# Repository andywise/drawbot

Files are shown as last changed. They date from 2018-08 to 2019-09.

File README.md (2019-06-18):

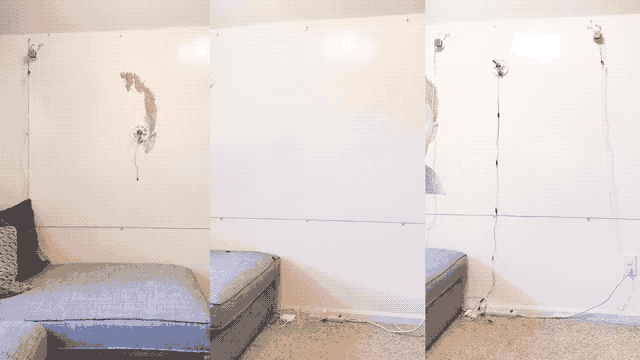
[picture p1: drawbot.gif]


# Drawbot ✏️🤖

Drawing robot capable of rendering SVG paths over WebSockets. Powered by a Raspberry Pi running Node.js.

## Parts List
### Printable Parts
* [Motor Mounts](https://www.thingiverse.com/thing:3054707) (two of each)
* [Electronics Case](https://www.thingiverse.com/thing:3058312)
* [Pen Holder Gondola](https://www.thingiverse.com/thing:372244)
* [Servo Horn Extension](https://www.thingiverse.com/thing:2427037)

### Everything Else (~$150 or less)

* [NEMA 17 Stepper Motors, 36.8oz.in 12v 0.4a](https://www.amazon.com/Stepping-Motor-26Ncm-36-8oz-Printer/dp/B00PNEQ9T4) (need 2) - $23.98
* [Suction Cup with Quick Release](https://www.harborfreight.com/suction-cup-with-quick-release-62715.html) (x2) - $5.98
* [Spiderwire 80-pound fishing line](https://www.amazon.com/gp/product/B00LDYLVVO/ref=oh_aui_search_detailpage?ie=UTF8&psc=1) - $17.56
* [Micro USB cable 10-ft. 2-pack](https://www.amazon.com/Android-Extremely-Durable-Charging-Generation/dp/B01NAG0YPD/ref=sr_1_8) - $8.99
* [Micro USB breakout 10-pcs](https://www.amazon.com/MagiDeal-10pcs-Female-Pinboard-2-54mm/dp/B0183KF7TM/ref=sr_1_4) (only need 2) - $6.59
* [USB type a female breakout 2-pack](https://www.ebay.com/itm/USB-2-0-Type-A-Female-Breakout-Board-2-54mm-Header-Gold-plated-Pack-of-2/302540094106) - $4.50
* [Raspberry Pi Zero W](http://www.microcenter.com/product/486575/Zero_W) - $10)
* [Easydriver Stepper Motor Driver](https://www.amazon.com/Cylewet-Easydriver-Stepper-Headers-Screwdriver/dp/B073D4H4F4/ref=sr_1_cc_1) (2-pack) - $9.99
* [SG92R](http://www.microcenter.com/product/454408/Micro_Servo) Micro Servo motor - $6.99
* [6003zz bearing 17x35x10](https://www.amazon.com/VXB-6003ZZ-Bearing-17x35x10-Shielded/dp/B002BBCO32/ref=sr_1_1) (need 2) - $11
* [10pcs 500mm 3-pin servo extensions](https://www.amazon.com/White-Terminal-Female-Extension-Airplane/dp/B01HLUZO4S/) (need several) - $7.69
* [2.1mm x 5.5mm barrel jack 15pcs](https://www.amazon.com/15PCS-Power-Socket-Barrel-Type-DC-005/dp/B00W944ACE/ref=sr_1_5) (need 1) - $7.59
* [12v 1a power adapter 2.1mm/5.5mm lead](https://www.amazon.com/Dericam-Power-Adapter-Supply-1000mA/dp/B01N3SNRE4/ref=sr_1_3) - $9.99
* [USB Micro Power Adapter](https://www.amazon.com/Keyestudio-Raspberry-Supply-Adapter-Charger/dp/B073RBXX2G/ref=sr_1_20) - $5.99
* [Pololu Universal Mounting Hub for 5mm shaft, #4-40 holes (2-pack)](https://www.pololu.com/product/1203) - $11.44
* [USB fan (40mm)](https://www.amazon.com/gp/product/B071JB9WYB/) - $7.99
* \#8-32 x 1-5/8 in. Eye Bolts (2-pack) - $0.98
* 8 screws for spools (#4-40 x ~½")
* 8 screws for motors (M3-.50 x 6mm metric machine screws)
* 1-2 small screws for gondola to secure pen/marker
* [Mounting Putty](https://www.amazon.com/Loctite-Fun-Tak-Mounting-2-Ounce-1087306/dp/B001F57ZPW) - $4.87
* Standard wire or jumper wires (and headers for components if using jumpers)
* Dry erase markers (or other drawing implements)
* Micro SD card (class 10 or better)

## Wiring

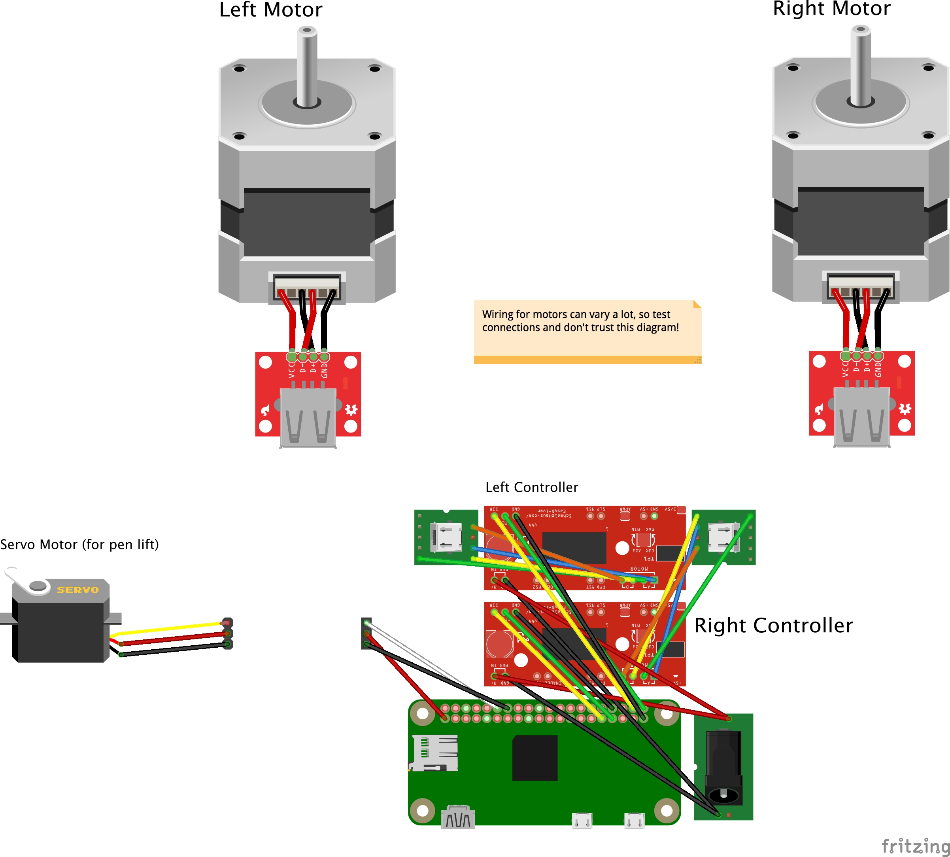
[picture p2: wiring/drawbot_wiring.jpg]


## Hardware Assembly

Thank you to the kind people at the Johnson County Library's Black & Veatch [MakerSpace](https://www.jocolibrary.org/makerspace) for documenting the assembly process at [instructables.com](https://www.instructables.com/id/Drawbot/).

## Raspberry Pi Zero W Basic Setup
1. **Download and install [Etcher](https://etcher.io/)**.
2. **Download and install latest [Raspbian OS](https://www.raspberrypi.org/downloads/raspbian/)** and flash it onto your SD card with Etcher.
3. **Enable SSH** by adding a blank file named `ssh` (no extension) to the `boot` directory on the Pi's SD card. (Last tested with Raspbian Stretch Lite 2018-06-27 version.)
4. **Set up Wifi** by adding a file named `wpa_supplicant.conf` to the same `boot` directory with the following contents (replace `MySSID` and `MyPassword` with your credentials):  
	```
	ctrl_interface=DIR=/var/run/wpa_supplicant GROUP=netdev
	update_config=1
		
	network={ 
		ssid="MySSID" 
		psk="MyPassword" 
	}
	```

## Software Prerequisites
From a device connected to the same network as the Drawbot Pi, SSH into the Pi with `ssh pi@raspberrypi.local`. The default password is `raspberry`.

Then, on the Drawbot Pi:

1. **Update, upgrade, and install NPM, Git.** (Automatically answer "yes" to everything.):
	* `sudo apt-get update`
	* `sudo apt-get upgrade`
	* `sudo apt-get install npm`
	* `sudo apt-get install git`

2. **Install Node.js.**
	* `sudo npm install -g n` (Install **n** for node.js version management. [github.com/tj/n](https://github.com/tj/n))
	* `sudo n stable` (Install latest stable version of Node.js. Last tested with v10.8.0)

3. **Upgrade NPM.** (and remove old apt-get version).
	* `sudo npm install npm@latest -g`
	* `sudo apt-get remove npm`
	* `sudo reboot` (After rebooting, you'll have to SSH into the Pi again.)

4. **Install pigpio C library.** [npmjs.com/package/pigpio](https://www.npmjs.com/package/pigpio)
	* `sudo apt-get install pigpio` (Only if you're using Raspbian *Lite*.)
	* `npm install pigpio`

## Installation
On the Drawbot Pi:

1. `git clone https://github.com/andywise/drawbot.git` to clone this repository.
2. `cd drawbot`
3. `npm i`

## Use
On the Drawbot Pi:

* Run `npm start` or `sudo node draw.js` to start the Drawbot controller.

## Controlling the Drawbot
On a device connected to the same local network as the Drawbot Pi:

* Go to [raspberrypi.local/control](http://raspberrypi.local/control) to access the Drawbot control interface.
* Use the "bullseye" interface to manually position the gondola, or raise/lower the pen/marker.
* Use the settings panel to configure the Drawbot's `D`, `X`, and `Y` values (see "Configuration" below).
* Drag and drop an SVG file onto the control interface to send artwork to the Drawbot!

### SVG Artwork Notes:
* **Only the first `<path>` element will be drawn**, so if necessary, combine artwork into a single compound path.
* The Drawbot will scale artwork so that **1 pixel = 1 millimeter**.

## Configuration
* **Enter value for `D`:** measure distance between string starting points (in millimeters).
* **Enter starting `X` and `Y` values:** measure distance from left and top (respectively) of left string starting point to initial pen position (also in mm).
* Note: Values will be stored in the `config.json` file.

## Rendering Raster Artwork (Coming Soon!)
* For now, go check out ["TSP Art."](https://wiki.evilmadscientist.com/TSP_art)

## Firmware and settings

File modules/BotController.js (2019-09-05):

var Gpio = require('pigpio').Gpio
var cBezier = require('adaptive-bezier-curve')
var qBezier = require('adaptive-quadratic-curve')
var svgParse = require('svg-path-parser')
var arcToBezier = require('./arcToBezier')// copied from svg-arc-to-bezier npm library, because it uses es6 import instead of require

var BotController = (cfg) => {

    var bc = {}
    var config = cfg.data


    /////////////////////////////////
    // MAIN SETUP VARIABLES
    bc._BOT_ID      = config.botID            // || 'drawbot'
    bc._DIRSWAP     = config.swapDirections   // || [true, true]
    bc.baseDelay    = config.baseDelay        // || 2
    bc._D           = config.d                // || 1000// default distance between string starts
    bc.startPos     = config.startPos         // || { x: 100, y: 100 }
    bc.stepsPerMM   = config.stepsPerMM       // || [5000/500, 5000/500] // steps / mm
    bc.penPause     = config.penPauseDelay    // || 200 // pause for pen up/down movement (in ms)


    /////////////////////////////////
    // GPIO SETUP
    var gmOut = {mode: Gpio.OUTPUT}
    var dirPins = [
        new Gpio(config.pins.leftDir, gmOut),
        new Gpio(config.pins.rightDir, gmOut)
    ]
    var stepPins = [
        new Gpio(config.pins.leftStep, gmOut),
        new Gpio(config.pins.rightStep, gmOut)
    ]
    // set up servo GPIO pin
    var servo = new Gpio(config.pins.penServo, gmOut)

    // ^ Step resolution Pins
    const leftMotorMs1= new Gpio(config.stepResolutionPins.leftMotor.ms1, gmOut)
    const leftMotorMs2= new Gpio(config.stepResolutionPins.leftMotor.ms2, gmOut)
    const leftMotorMs3= new Gpio(config.stepResolutionPins.leftMotor.ms3, gmOut)
    const rightMotorMs1= new Gpio(config.stepResolutionPins.rightMotor.ms1, gmOut)
    const rightMotorMs2= new Gpio(config.stepResolutionPins.rightMotor.ms2, gmOut)
    const rightMotorMs3= new Gpio(config.stepResolutionPins.rightMotor.ms3, gmOut)

    // ^ Step resolution settings
    // * Were configuring our driver for an Eighth Step resolution. Also note that these pinouts
    // * correspond to the A4988 StepStick stepper motor driver:
    // ? https://www.pololu.com/product/1182
    // 
    // * We're not adjusting the values on the fly so they can be set here and not touched, but if your resolution
    // * needs to vary at runtime you can adjust the values of these pins. More information 
    // * on pin configurations can be found here:
    // ? https://howtomechatronics.com/tutorials/arduino/how-to-control-stepper-motor-with-a4988-driver-and-arduino/
    leftMotorMs1.digitalWrite(1)
    leftMotorMs2.digitalWrite(1)
    leftMotorMs3.digitalWrite(0)
    rightMotorMs1.digitalWrite(1)
    rightMotorMs2.digitalWrite(1)
    rightMotorMs3.digitalWrite(0)

    /////////////////////////////////
    // CONTROLLER VARIABLES

    // TODO: isolate private/public stuff

    bc.pos = {x:0, y:0}
    bc.penPos = 0
    bc.paused = false

    // string length stuff
    bc.startStringLengths = [0, 0]
    bc.stringLengths = [0, 0]
    bc.startSteps = [0, 0]
    bc.currentSteps = [0, 0]
    bc.stepCounts = [0, 0]
    bc.steppeds = [0, 0]
    bc.paths = []
    bc.drawingPath = false


    /////////////////////////////////
    // HARDWARE METHODS

    bc.updateStringLengths = () => {
        bc.startStringLengths = [
            Math.sqrt( (bc.startPos.x * bc.startPos.x) + (bc.startPos.y * bc.startPos.y) ),
            Math.sqrt( ( (bc._D - bc.startPos.x) * (bc._D - bc.startPos.x) ) + (bc.startPos.y * bc.startPos.y) )
        ]
        bc.stringLengths = [bc.startStringLengths[0],bc.startStringLengths[1]]
        bc.startSteps = [Math.round(bc.stringLengths[0] * bc.stepsPerMM[0]), Math.round(bc.stringLengths[1] * bc.stepsPerMM[1])]
        bc.currentSteps = [bc.startSteps[0], bc.startSteps[1]]

        console.log('bc.startPos',JSON.stringify(bc.startPos))
        console.log('startStringLengths', JSON.stringify(bc.startStringLengths))
        return bc.startStringLengths
    }

    bc.setStartPos = (data) => {
        cfg.data.startPos.x = bc.startPos.x = Number(data.x)// set values and store in config
        cfg.data.startPos.y = bc.startPos.y = Number(data.y)// set values and store in config
        cfg.save()// save to local config.json file
        bc.updateStringLengths()
    }
    bc.setD = (data) => {
        cfg.data.d = bc._D = Number(data)// set value and store in config
        cfg.save()// save to local config.json file
        bc.updateStringLengths()
    }

    bc.pen = (dir) => {
        bc.penPos = dir
        // 0=down, 1=up
        // 544 to 2400
        var servoMin = 544
        var servoMax = 2400
        var servoD = servoMax-servoMin
        var servoUpPos = servoMin+Math.floor(servoD*0.35)
        var servoDnPos = servoMin
        if(dir){
            // lift pen up
            // console.log('up')
            servo.servoWrite(servoUpPos)
        }else{
            // put pen down
            // console.log('down')
            servo.servoWrite(servoDnPos)
            // servo.digitalWrite(0)
        }
    }
    bc.penThen = (dir, callback) => {
        if(dir!=bc.penPos){
            bc.pen(dir)
            if (callback!=undefined){
                setTimeout(callback, bc.penPause)
            }
        }else{
            callback()
        }
    }

    bc.makeStep = (m, d) => {
        // console.log('step',d)
        if(bc._DIRSWAP[m]) d = !d// swap direction if that setting is on
        dirPins[m].digitalWrite(d)
        stepPins[m].digitalWrite(1)
        setTimeout(function(){
            stepPins[m].digitalWrite(0)
        },1) 
    }

    // TODO: This could move to a python script for faster execution (faster than bc.baseDelay=2 miliseconds)
    bc.rotateBoth = (s1, s2, d1, d2, callback) => {
        // console.log('bc.rotateBoth',s1,s2,d1,d2)
        var steps = Math.round(Math.max(s1,s2))
        var a1 = 0
        var a2 = 0
        var stepped = 0

        var doStep = function(){
            if(!bc.paused){
                setTimeout(function(){
                    // console.log(stepped,steps)
                    if(stepped<steps){
                        stepped++
                        // console.log('a1,a2',a1,a2)

                        a1 += s1
                        if(a1>=steps){
                            a1 -= steps
                            bc.makeStep(0,d1)
                        }

                        a2 += s2
                        if(a2>=steps){
                            a2 -= steps
                            bc.makeStep(1,d2)
                        }

                        doStep()

                    }else{
                        // console.log('bc.rotateBoth done!')
                        if (callback!=undefined) callback()
                    }
                }, bc.baseDelay)
            }else{
                // paused!
                console.log('paused!')
                bc.paused = false
            }
        }
        doStep()
    }
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

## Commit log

2018-08-20 readme update: parts list, wiring, raster art
    [drawbot_wiring.fzz]
2019-06-18 Added instructables link in Hardware Assembly
2019-08-30 change hard-coded delay to 2ms from 1ms
    Fixes an error on some motor configurations.
2019-09-05 allow each motor to swap directions independently
    [BotController.js]
2019-09-05 swapDirections as array not boolean
    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
